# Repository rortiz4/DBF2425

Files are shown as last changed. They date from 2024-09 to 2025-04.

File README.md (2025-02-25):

# DBF2425
Any hardware or software design files for DBF 24-25 will be uploaded here

## Control System Software Flowchart
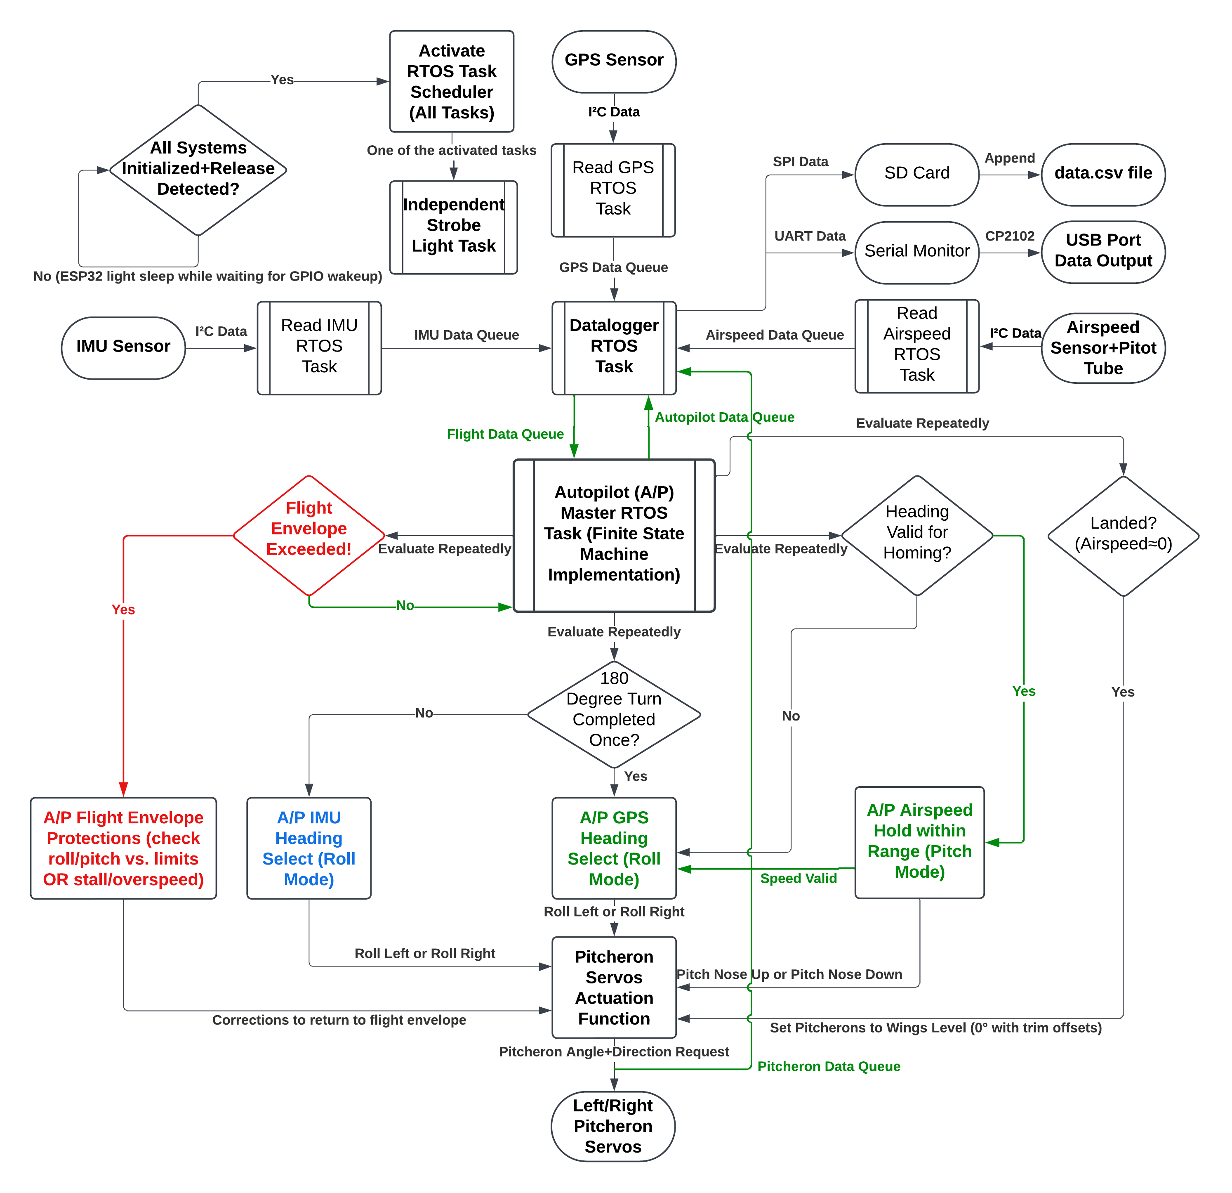
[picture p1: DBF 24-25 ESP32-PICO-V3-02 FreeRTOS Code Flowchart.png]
DBF 24-25 ESP32-PICO-V3-02 FreeRTOS Code Flowchart


## Power Path
DBF 24-25 System Power Path

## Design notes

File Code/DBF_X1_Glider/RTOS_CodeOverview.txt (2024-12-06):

RTOS Features Implemented:
(Sensors):
- IMU
- Differential Pressure (Pitot Tube/Airspeed)
- GPS

CPU Usage:
- CPU0: All sensor reading tasks are on this since they need the I2C Mutex anyway, so only one task runs at a time (no parallel benefit)
- CPU1: Data Logging task since after receiving queue data, it can immediately start saving data while the sensors are collecting the next dataset

Tasks (4, each with 4096 bytes stack size [lower = faster sampling]):
- Initialize All Sensors... Don't need RTOS for this
- Initialize SD Card / Data Logging... Don't need RTOS for this
- Read IMU (CPU0)
- Read Airspeed Sensor (CPU0)
- Read GPS Data (CPU0)
- Log Data to CSV File (CPU1)

Queues (3):
- IMU Data Queue Send => Logging Task Queue Receive
- Airspeed Data Queue Send => Logging Task Queue Receive
- GPS Data Queue Send => Logging Task Queue Receive

Timers: None (Could make one for built-in LED just for fun)

Task Control (Suspend/Resume):
- SUSPEND TASK: IMU Read once queue is filled with fresh data
- SUSPEND TASK: Airspeed Read once queue is filled with fresh data
- SUSPEND TASK: GPS Read once queue is filled with fresh data
- RESUME TASKS ABOVE: As soon as each queue is emptied by logging task => Each Sensor Reading Task (only log after all sensors have been polled once)

Mutex(1) + Binary Semaphores(3):
- I2C Bus MUTEX: Ensures only one sensor accesses the I2C bus at any given time.
Each sensor task attempts to take it once in the infinite loop
While waiting for data, each sensor task gives back the semaphore in a sub-infinite (while !data) loop
If there is data, the semaphore is taken by the sensor that got data
After pulling the data, the semaphore is given back (and task suspends).
- IMU Done Reading Semaphore => Signals Logging Task that queue is filled with fresh data
- GPS Done Reading Semaphore => Signals Logging Task that queue is filled with fresh data
- Pitot Tube Sensor Done Reading Semaphore => Signals Logging Task that queue is filled with fresh data

Files:
- main.cpp: self-explanatory starting point for program (as small as possible but #includes a lot)
- sensors.h+sensors.cpp: Code for initializing Serial, I2C, and all sensors (not with RTOS) + Task Functions to read each sensor individually + structs for each sensor's data/types
- datalogger.h+datalogger.cpp: Code for initializing the SD Card and logging (.csv) data to Serial Monitor and/or SD Card file.
- Tasks, Queues, and Semaphores + their associated handles, declarations, and definitions are stored in tasks.h/tasks.cpp, queues.h/queues.cpp, and semaphores.h/semaphores.cpp

(Outputs):
- SD Card .csv file writing
- Serial Monitor Printing
- LED Toggle after every .csv file entry.

Sample Rate Estimates:
- IMU Alone: 15Hz
- Airspeed Sensor Alone: 145Hz
- All Sensors Together: 10Hz originally (excluding GPS)
- After Optimizations (lower stack size, using dual core, etc.): 15.34Hz rate (excluding GPS)

TODO (as of 12/04/2024):
New Tasks:
- Release Detection: Detect when IOXX has been pulled LOW/HIGH
- Strobe LED: Blink the LED (IOXX)
- 180 Degree Turn (any angle allowed actually): Counter-Rotate Pitcherons. Compares current bearing vs. current bearing-180 degrees
- Level Roll: Counter-Rotate to maintain level flight (+/-5 deg of roll allowed). If bank angle exceeds +/-5 degrees, rotate back to center
- Level Pitch: Rotate pitcherons together to maintain airspeed target (pitch up to slow down, down to speed up)
Note: Level Roll has priority over Level Pitch (semaphore required). Could combine 3 tasks above into 1 Autopilot task.

New Queues:
- Flight Data (source: datalogger task function, sinks: 180 degree turn and level flight OR Autopilot tasks)
- Autopilot Data (source: Autopilot task, sink: datalogger)
- Servo Angle Data (source: actuate_pitcherons in pitcherons_servos.cpp, sink: datalogger task function)

New Semaphores:
- 180 Degree Turn Semaphore (180 degree turn task gives, level roll task takes)
- Level Roll Semaphore (Level roll task gives, Level Pitch task takes)
- OR just ONE Autopilot Done Semaphore for datalogger

New Files:
- pin_map.h: consolidates all physical I/O pin assignments (from PCB schematic)
- pitcherons_servos.h, pitcherons_servos.c: contain code to initialize servos and actuate to an angle (no direct tasks)
Note: servos.h will contain struct to hold servo angle data (int angle and int act_type_direction)
- strobe.h, strobe.cpp: contain code to initialize Addon strobe LED and task function for blinking (+ Data struct)
- autopilot.h, autopilot.cpp: contain task functions that actually perform turns and pitch adjustments based on sensor data.

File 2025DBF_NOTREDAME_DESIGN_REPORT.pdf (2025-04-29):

University of Notre Dame | Page 2 of 60

## Contents

1 Executive Summary | 4
2 Management Summary | 5
3 Conceptual Design | 6
4 Preliminary Design | 15
5 Detailed Design | 32
6 Manufacturing Plan | 48
7 Testing Plan | 53
8 Performance Results | 57
9 Bibliography | 60

University of Notre Dame | Page 3 of 60

## Acronyms and Symbols

α - Angle of Attack

AR - Aspect Ratio

ARV T - Aspect Ratio of the Vertical Tail

β - Sideslip Angle

bW - Wing Span

bHT , bV T - Horizontal, Vertical Tail Spans

CA - Cyanoacrylate (glue)

CAD - Computer Aided Design (Software)

CAM - Computer Aided Manufacturing

CD - Coefficient of Drag

CL - Coefficient of Lift

CLmax
- Maximum Coefficient of Lift

c¯W - Mean Aerodynamic Chord

CHT , CV T - Horizontal, Vertical Tail Coefficients

CF - Carbon Fiber

CG - Center of Gravity

Cm - Pitching Moment Coefficient

Cmα

- Slope of the Cm vs α curve

CNC - Computerized Numerical Control

D - Drag

DBF - Design, Build, Fly

e - Oswald Efficiency Factor

EIH - Engineering Innovation Hub

ESC - Electronic Speed Control

FEA - Finite Element Analysis

FoM - Figures of Merit

g - Acceleration Due to Gravity

GM - Ground Mission

GM - Ground Mission Score

GPS - Global Positioning System

I - Second Moment of Inertia

IMU - Inertial Measurement Unit

LHT , LV T - Horizontal, Vertical Tail Moment Arm Distance

L - Lift

LiPo - Lithium Polymer

M1 - Mission 1

M2 - Mission 2

M3 - Mission 3

M1 - Mission 1 Flight Score

M2 - Mission 2 Flight Score

M3 - Mission 3 Flight Score

MATLAB - Matrix Laboratory

Mmax - Maximum Moment

n - Load Factor

Nc - Number of Aircraft Components

NACA - National Advisory Committee for Aeronautics

ND DBF - Notre Dame Design, Build, Fly

PCB - Printed Circuit Board

PID - Proportional Integral Derivative

PWM - Pulse Width Modulation

Q&A - AIAA Rules Clarification Question and Answer

RC - Radio Controlled

Re - Reynold’s Number

RK4 - 4th Order Runge-Kutta Method

RPM - Revolutions Per Minute

SW - Planform Area

SHT - Area of Horizontal Tail

SV T - Area of Vertical Tail

SM - Static Margin

T - Thrust

V - Airspeed

Vclimb - Climb Velocity

Vland - Landing Velocity

Vs - Stall Speed

VHT - Horizontal Tail Volume Ratio

W - Weight

XCG - x-location of Center of Gravity

XNP - x-location of Neutral Point

XFLR5 - XFoil Low Reynolds Version 5

XPS - Extruded Polystyrene

µ - Kinematic Viscosity

ϕ - Bank Angle

ρ - Density of Air

σ - Bending Stress

τ - Flap Effectiveness Parameter

Λt/c - Sweep of the Maximum Thickness Over the Chord Line ψ˙
- Turn Rate

University of Notre Dame | Page 4 of 60

## 1 Executive Summary

The following report outlines the process followed by the Notre Dame Design Build Fly team to prepare for entry into the 2025

American Institute of Aeronautics and Astronautics Design/Build/Fly Competition. The team has designed and built a radio-

controlled aircraft and an X-1 test vehicle to complete three flight missions and one ground mission, as described in the AIAA

competition rules [1]. To achieve this, the main aircraft was optimized to carry a large payload for Mission 2 and to have high

endurance for Mission 3. The X-1 test vehicle was designed to execute a flight path to land in the maximum scoring zone.

The main aircraft features a low wing design with a puller configuration and tail dragger landing gear. The empennage consists

of a conventional tail connected to a tapered section of the fuselage by a boom. The low wing design was selected to maximize

maneuverability, while a dihedral wing angle was incorporated to improve stability. The single motor puller configuration was

chosen for its efficiency and minimal interference with mission objectives. A tail dragger configuration was chosen for its reduced

weight and drag, and the boom tail further minimizes weight and surface drag from the rear section of the aircraft. The fuselage

cross section is a Norman window shape, providing both a simplified interface for external components and reduced drag with

its curved roof. This configuration is shown in Figure 1. The fuselage and wings are primarily constructed from wood due to

its lightweight properties and ease of manufacturing. Select structural components, such as the spars and boom tail, are made

from carbon fiber, while the wingbox is machined from aluminum. Removable pylons can be attached to the wing tips to hold fuel

tanks, which are loaded with a combination of concrete powder and steel weights. The X-1 test vehicle is attached to the bottom

of the fuselage below the wingbox, with its vertical stabilizer passing through a bomb bay door in the fuselage floor. This location

was chosen to minimize shifts in the aircraft’s center of gravity when the vehicle is dropped. The X-1 test vehicle has a low wing

configuration with a conventional tail, both chosen for their reliable stability and low weight, and is controlled by a custom system

that rotates the wings to function as either ailerons or an elevator. Control inputs are informed by a GPS, an IMU, and a Pitot

tube. The X-1 test vehicle is constructed from carbon fiber and foam to minimize weight.

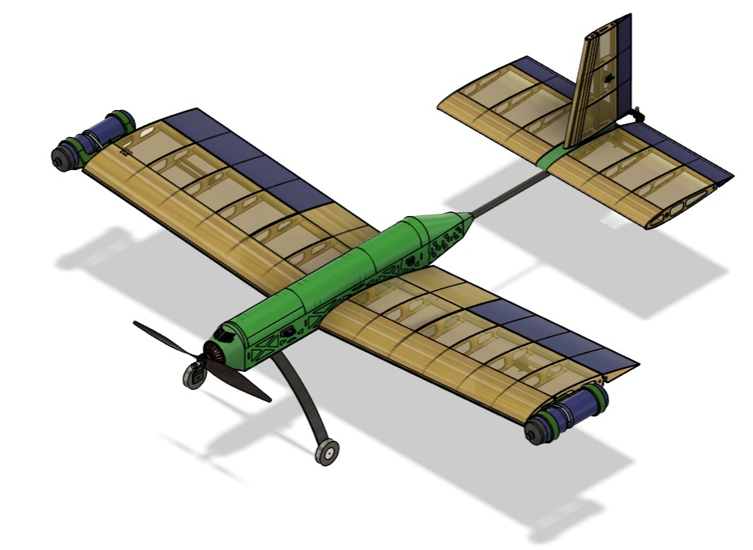
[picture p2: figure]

Figure 1: ND DBF 2025 Aircraft

Scoring analysis was conducted to determine the optimal air-

craft configuration for maximizing payload weight, lap time for

M2, and endurance for M3. Following scoring analysis and

considering lessons learned from test flights, the team chose

to carry a 8 lb payload and have a total flight time of 87 sec-

onds for M2. For M3, the aircraft is designed to complete 9

laps, with the X-1 test vehicle weighing 0.29 lbs to aim for the

2.5-point bonus zone. The pylons and X-1 attachment mech-

anism were designed to minimize installation time for a higher

GM score while remaining securely attached throughout the

flight. To improve on detailed designs the team planned five

flight tests of iterative aircraft. In addition, structural and

propulsion tests were planned to inform performance of spe-

cific components. Early flight tests led to a major redesign to

improve the landing performance of the aircraft. Subsequent

tests have demonstrated that the current design track is able

to perform and excel in all scoring missions.

University of Notre Dame | Page 5 of 60

## 2 Management Summary

### 2.1 Team Organization

Figure 2: Team Organizational Structure

The Notre Dame DBF team consists of approx-

imately 25 undergraduate members, with about

15 returning and 10 new members. The overall

organizational structure of the team is illustrated

in Figure 2. The general membership of the team

is divided into three main design squads: Aerody-

namics, Structures and Manufacturing, and Pay-

load. The Aerodynamics squad is responsible for

the aerodynamic parameters of the plane, includ-

ing lifting surface design, propulsion design, and

stability analysis. The Structures and Manufac-

turing squad is responsible for the structural in-

tegrity of all components, fuselage design, and

manufacturing process selection. The Payload

squad is responsible for all payload systems,

avionics, and mechanisms necessary for mission completion. It is notable to mention that the X-1 test vehicle design is shared be-

tween the three squads rather than being a payload-specific task. Each squad is run by a lead who is responsible for conducting

meetings and ensuring that squad-specific design requirements are met in a timely manner. The Structures and Manufacturing

squad is managed by co-leads to handle the large number of responsibilities and to provide mutual support and oversight. Each

squad lead is supported by sub-leads, who act as assistants for leads instead of having specific tasks. Sub-leads help with both

design and administrative tasks, ensuring the smooth operation of the squad and serving as reliable team members. All three

squads are overseen by the Project Manager and the Chief Engineer. The Project Manager is responsible for keeping the team on

schedule, within budget, and focused by setting team goals, managing budget constraints, organizing meetings, and purchasing

supplies. The Chief Engineer oversees top-level requirements and makes all final design decisions. The Chief Engineer also

provides design requirements to the squads, and the Project Manager ensures those requirements are efficiently completed. The

whole team is advised by Industry and Faculty advisors during design reviews. Additionally, the team receives empirical feedback

from a non-student pilot during test flights. The team also includes several auxiliary roles to address areas of past weaknesses.

The Research and Development Officer is responsible for enhancing the team’s performance potential by improving subsystems

and processes. The Chief Technical Editor oversees the organization of all reports and proposals. The Media Editor manages

the team’s social media presence and recruits new members.

### 2.2 Milestones

The Project Manager holds the team to the schedule outlined in Figure 3. Squad tasks are completed during weekday meetings,

and a full team meeting is held on Sundays to maintain communication between squads. The schedule has been adjusted

throughout the year, mainly due to flight tests that resulted in minimal structural damage. This led to small repairs and flights

being moved to the following week to collect more information.

University of Notre Dame | Page 6 of 60

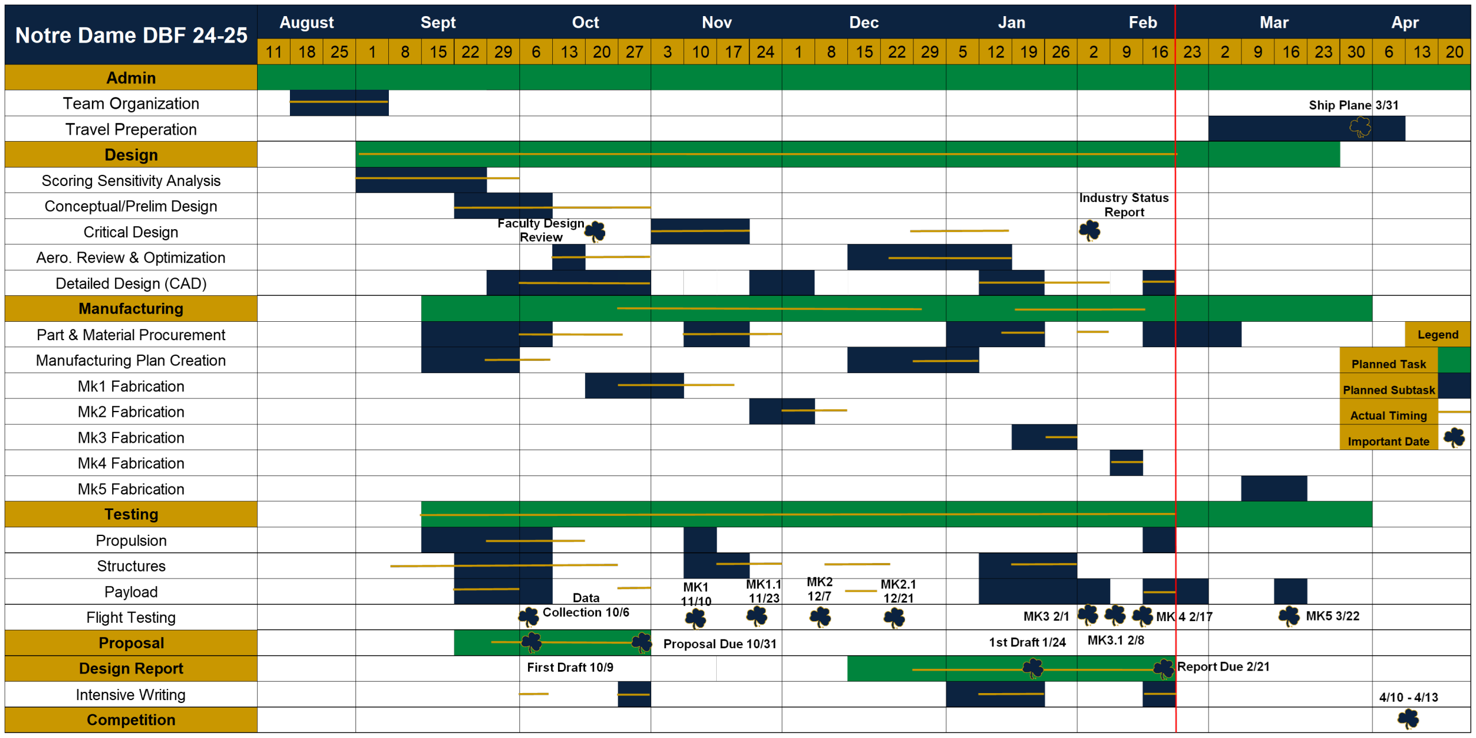
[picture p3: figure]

Figure 3: 2024-2025 Gantt Chart

## 3 Conceptual Design

### 3.1 Engineering Requirements

ND DBF’s engineering requirements were developed using a careful analysis of mission requirements, obtained through a thor-

ough review of the rules and Q&As released by AIAA.

### 3.1.1 Problem Statement

ND DBF must design, build, and fly an airplane to execute an X-1 Supersonic Flight Test Program, completing three assigned

flight missions and a ground mission in order to ensure airworthiness, test payload capacity and speed, and demonstrate the

ability to effectively deploy an X-1 test vehicle from the main aircraft.

### 3.1.2 General Aircraft Requirements and Restrictions

AIAA has provided comprehensive guidelines through the official rules and subsequent Q&A sessions. These guidelines outline

design constraints, performance expectations, and payload regulations for the ND DBF team. Table 1 details the requirements

that the team considers central to the aircraft design and their impact on each ND DBF squad.

University of Notre Dame | Page 7 of 60

Table 1: Mission Requirements and Squad Impact

Category | Requirement | Aerodynamics Squad | Struct. & Manu. Squad | Payload Squad
Aircraft Design | The maximum airplane wingspan is six feet. | Design tradeoff between wing area and aspect ratio. | The structure must endure a maximum span of six feet. | Minimal Implications.
| Aircraft must be capable of completing all three missions. | Plane aerodynamic design must allow completion of all three missions. | Plane structural design must allow completion of all three missions. | Payload design must allow completion of all three missions.
| Aircraft must be flown in same configuration for all three missions excluding payloads. | Aerodynamic design must complete all three missions without changes. | Structural design must complete all three missions without changes. | Payload design must complete all three missions without changes.
| No structure or components may be dropped from the plane during flight excluding the X-1 test vehicle in M3. | Minimal Implications. | No loose components are permitted. | X-1 test vehicle must be secured when attached to main aircraft.
| Commercially available propeller, battery, and motor must be used. | Only commercially available propulsion systems can be considered for the aerodynamic design. | Minimal Implications. | Minimal Implications.
| Aircraft must pass a wing tip test in the heaviest flight condition. | Minimal Implications. | Plane structural design must pass a wing tip test at maximum flight weight. | Minimal Implications.
| Aircraft can be any configuration other than rotary and lighter than air. | Aircraft must be designed with traditional fixed wings. | Minimal Implications. | Minimal Implications.
Assembly | Assembly work on the aircraft must be completed with the plane in the upright, parking position. The aircraft cannot be picked up, rotated, or put in any other position. The only exception to this is the ability to add blocks underneath the wheels of the landing gear to allow for access underneath the plane if need be. | Minimal Implications. | Structural members and hatches must be placed carefully to facilitate assembly and loading in the upright configuration. | Payload components must be designed and placed to facilitate assembly and loading in the upright configuration.
| Aircraft will enter the staging area in the parking configuration with the propulsion battery and payload removed. Aircraft assembly and payload installation must be completed in less than five minutes by one person. | Minimal Implications. | Structural members and hatches must be placed carefully to facilitate assembly in less than five minutes. | Payload components must be designed and placed to facilitate assembly and loading in less than five minutes.
Flight Performance | Aircraft must have a successful landing to receive a score for the mission. | Aircraft must be designed to land at a velocity that is controllable for the pilot | Structure must withstand the force of landing without failure | Minimal Implications
| The airplane will use ground rolling takeoff and landing. | Wing, propulsion system, and weights must be selected to allow for rolling takeoff. Must take off in length of testing runway. | Aircraft structures must withstand the forces of extended takeoff and landing. | Minimal Implications.
| Fuel tanks can be any commercially available bottle as long as it has a screw-on lid. Bottle can be painted/decorated, but otherwise cannot be altered in any way. Bottle must have a minimum capacity of 16 oz. Bottle cannot be glass. | Bottle chosen must be as aerodynamic as possible. | Minimal Implications. | Fuel tank must be designed to meet the requirement.
| Fuel tank bottles can be filled with any amount of inert material to get the desired payload weight. | Design tradeoff between fuel tank weight and speed. | Minimal Implications. | Fuel tank must be strong enough to hold intended payload weight.
| At least two fuel tanks must be carried externally (minimum of 2 fuel tanks required). External fuel tanks must be identical. Internal fuel tank can differ from external. Internal fuel tank is optional. | Minimal Implications. | Fuselage and wings must be designed to withstand additional weight from fuel tanks. | Fuel tanks must be designed to be properly incorporated with aircraft, whether internal or external.
| External fuel tanks must be attached using detachable pylons. Pylons must hold fuel tank securely for all phases of flight. | Pylons should be as low-drag and light as possible since their weight will not affect mission score. | Minimal Implications. | Pylons must be secure enough to hold fuel tanks through all phases of flight. Also must design pylons to be detachable. Fuel tanks chosen must interface properly and securely with pylon.
| X-1 test vehicle must be attached to the plane and dropped at an altitude of 200-400 ft via command from the transmitter. | Minimal Implications. | Minimal Implications. | Must design a low-weight mechanism to hold and release the X-1 test vehicle on command/at altitude.
| Fuel tanks must be placed on either side of the X-1 test vehicle. | Minimal Implications. | Minimal Implications. | Fuel tank placement must be chosen properly to meet the requirement.
| After being dropped, the X-1 test vehicle must achieve stable flight after release from the airplane, execute a 180 degree turn, and then fly a descending pattern or orbit until landing on the ground. | X-1 test vehicle must be designed to achieve steady flight and required flight path. | Minimal Implications. | A mechanism for controlling the X-1 test vehicle must be designed to achieve flight requirements.
| X-1 test vehicle must have flashing lights/strobes which turn on only after release from plane and remain on through landing. Lights must be easily visible to flightline judge. | Minimal Implications. | X-1 test vehicle must protect necessary components for strobe light operation through landing. | X-1 test vehicle must be designed to meet this requirement.
| X-1 test vehicle cannot exceed 0.55 lbs in weight. | X-1 test vehicle aerodynamic surfaces must be light while still maintaining control authority. | Materials chosen for X-1 test vehicle must be light but strong enough to withstand flight loads. | X-1 test vehicle components and total weight must remain under 0.55

Payload

lbs in weight. 3.1.3 Mission Scoring Summary

AIAA has outlined the mission rules and scoring criteria. A brief description of the requirements for each mission, along with the

associated scoring equations, is shown in Table 2.

University of Notre Dame | Page 8 of 60

Table 2: Mission Scoring Summary

Mission | Description | Scoring
GM | Record time to install pylons, X-1 test vehicle with attachment mechanism, and fuel tanks. Verify function of all control surfaces and X-1 test vehicle release function. Aircraft enters staging area in M1 configuration before timer begins.
M1 | Delivery flight with no payload. Complete 3 laps of flight course within 5 minute time window. Complete a successful landing.
M2 | Captive carry flight with loaded fuel tanks and X-1 Vehicle payload. Complete 3 laps of flight course in shortest possible time. Carry X-1 and fuel tanks for duration of flight and successfully land.
M3 | Launch flight with unloaded fuel tanks, X-1 test vehicle, and payload. Complete maximum number of laps in 5 minute window. At beginning of final lap drop X-1 test vehicle prior to the upwind turn. Once dropped X-1 test vehicle must complete a 180° turn before landing in bonus point area. X-1 test vehicle strobe light must be on during descent and after landing, but never before. Primary aircraft must complete a successful landing.

### 3.1.4 Competition Scoring Summary

Table 3: Participation Scoring

Participation Score | Requirement

## 1 Attend Fly-off 2 Pass Tech Inspection 3 Attempt Flight Mission

The overall competition score is a combination of Mission Score, Report Score, and

Participation Score, P, further detailed in Table 3. Of note is that the Total Mission

Score is multiplied by the Report Score. The larger variance in Mission Score

means that it has a larger effect, however, the Report Score acts as a multiplier on

the performance of the team during the missions. The Total Report Score is split

into components for the proposal and design report as described in Equation (2).

Competition Score = Total Report Score × Total Mission Score + P | (1)
Total Report Score = (0.15 × Proposal Score) + (0.85 × Design Report Score) | (2)
Total Mission Score = M1 + M2 + M3 + GM | (3)

### 3.2 Scoring Sensitivity Analysis

After breaking down mission requirements into specific aircraft design criteria, the team analyzed this year’s critical scoring

parameters to optimize the wing and propulsion system for maximum performance. Using a MATLAB script, potential aircraft

configurations were generated by fixing the wingspan at the maximum allowable 6 ft and iterating over the wing aspect ratio

and payload weight [2]. Fixing the wingspan at 6 ft allowed for the design of efficient, high aspect ratio platforms, but was later

altered to accommodate the payload fuel tanks being attached at the wingtips. To account for scoring dependence on landing

location and weight, the X-1 test vehicle was treated as an additional 0.55 lbs in the total aircraft weight. The script estimated the

structural and electronics weights based on previous DBF aircraft and selected a propulsion system using a custom database of

manufacturer-provided data for motors, propellers, and batteries. Each configuration of aspect ratio, motor, propeller, and battery

was required to achieve three primary goals:

1. Attain a minimum static thrust-to-weight ratio of 1.2.
2. Fly for at least 5.5 minutes.
3. Take off within 250 ft (the length of the team’s test runway).

University of Notre Dame | Page 9 of 60

The thrust-to-weight ratio was chosen from a historical range of 0.8 to 1.2, with the upper limit selected to ensure sufficient

thrust to offset the added drag from the fuel tanks. Configurations meeting these criteria were deemed minimally viable for the

competition. Each viable configuration was mathematically simulated and scored using the M2 and M3 scoring equations, as well

as performance equations from Thomas Corke’s Design of Aircraft [3]. Figure 4 shows the flow of the scoring analysis script. The

results, illustrated in Figures 5 and 6, show each point representing a viable aircraft and propulsion configuration.

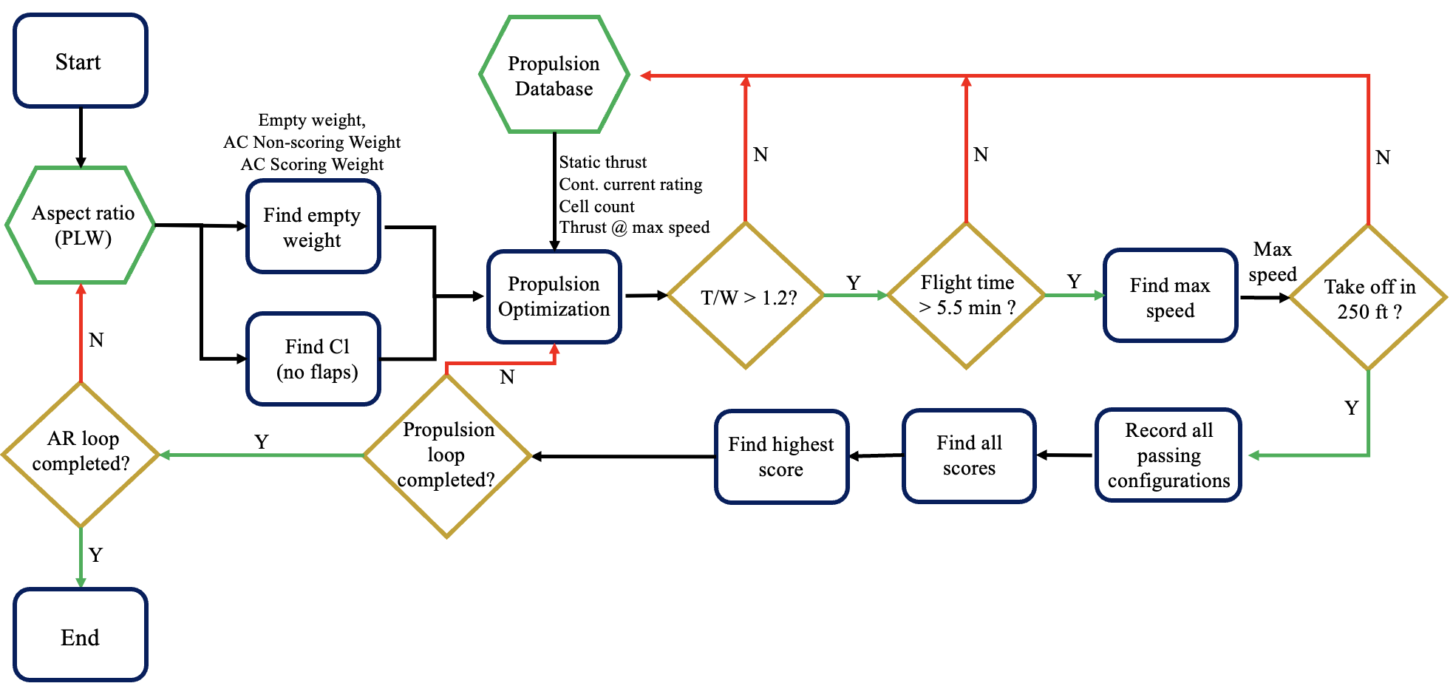
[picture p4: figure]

Figure 4: Flow Chart of ND DBF’s Scoring Analysis Script

After preliminary testing flights with failures resulting from an excessively high required landing speed, it was determined that

the original scoring strategy did not adequately take into account pilot controllability factors such as landing speed. Thus, the

scoring analysis code was altered to implement penalties for high landing and takeoff speeds. This was done by requiring

each configuration to have a maximum stall speed of 40 ft/s and capping the maximum wing area to 7.5 ft²
, both of which

were determined through ND DBF’s previous experience with successful flights, best manufacturing practices, and conventional

wisdom regarding RC aircraft. Once these penalties were implemented to ensure the selected design would be flyable by a pilot,

Figures 5 and 6 were created. Due to budget constraints, the team was unable to select a new motor for the aircraft and thus

decided to map the current motor to a new, winning configuration. In both figures, each minimally viable aircraft is plotted by its

maximum speed, determined by calculating the excess thrust of each aircraft and the speed at which it is minimized. For the

selected aircraft, the maximum velocity for each mission is indicated by a red X. However, cruise speed values, defined as the

flight speed when lift is equal to weight without any additional pitch control input, are generally much lower than the maximum

speed. The cruise speeds for each mission were calculated using Equation (4), where lift is assumed to equal aircraft weight.

L = W =

1
2
ρV ²CLSW | (4)

These values are shown for the given aircraft in Figures 5 and 6 as a black X. These velocity values are low relative to the

maximum velocity of the aircraft. However, based on previous year’s flight data, the team has determined that, by taking advantage

of pitch control and diving capability, the pilot can exceed this cruise value to roughly 95% of the maximum velocity of the aircraft.

This value, marked by the golden star in Figures 5 and 6, is the predicted competition lap velocity and is used for a majority of the

following analyses. The final results of the scoring analysis, including performance predictions and physical design parameters,

are shown in Tables 4 and 5.

University of Notre Dame | Page 10 of 60

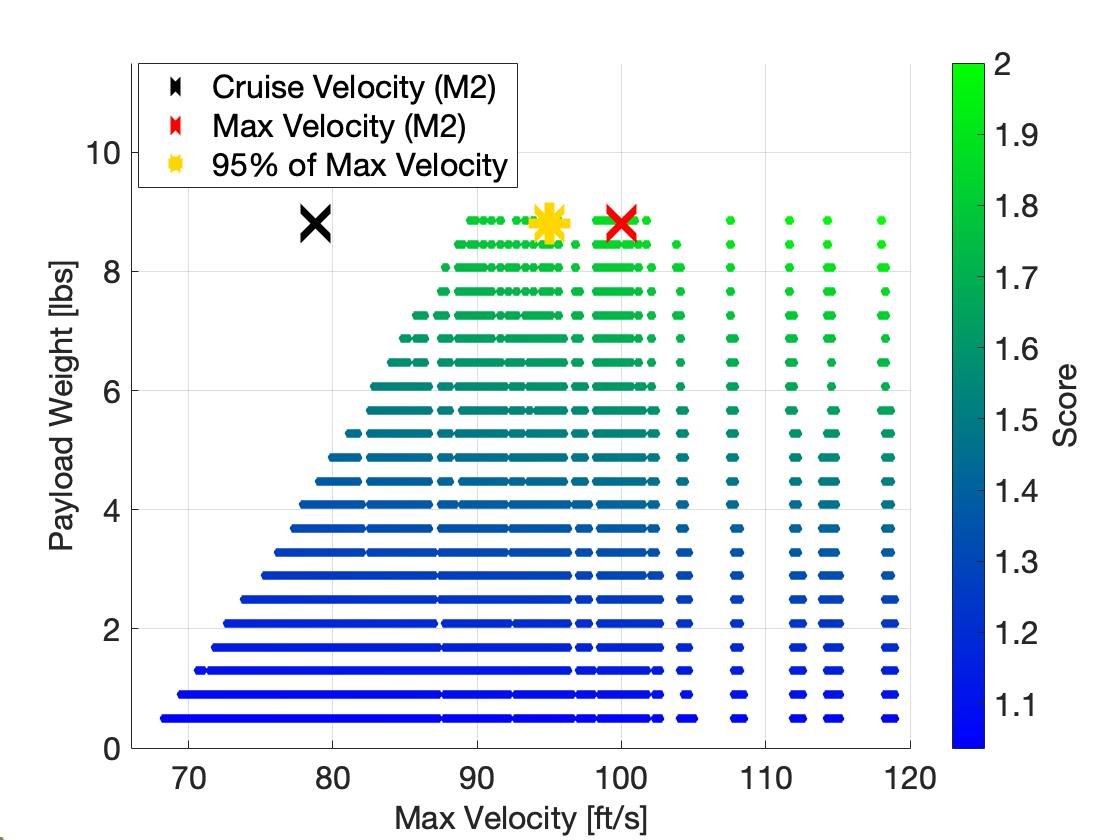
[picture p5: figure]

Figure 5: ND DBF M2 Scoring Analysis | Figure 6: ND DBF M3 Scoring Analysis

Table 4: Preliminary Scoring Parameters

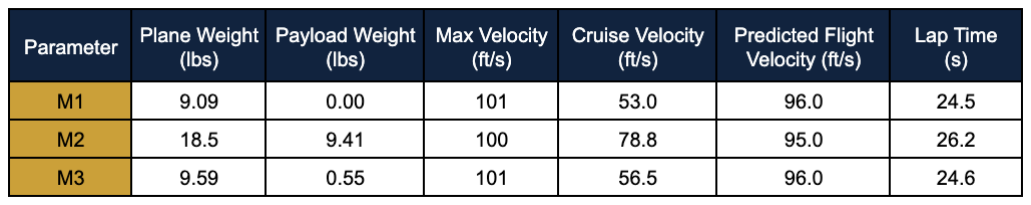
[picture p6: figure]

Table 5: Preliminary Design Parameters

### 3.3 Concepts Selection Process

To select the overall aircraft configuration, including the wing and empennage designs, the team utilized weighted decision

matrices to evaluate various options against Figures of Merit (FoM) determined by the design requirements. Every design option

was rated on a scale of 1 to 5 for each FoM, with the highest total score, a sum of the individual FoM scores multiplied by their

respective weights, representing the best choice. The assigned weight and scores were selected based on knowledge from

the team’s past airplane performance, additional research, and the performance of other teams’ past aircraft, with the selected

configuration for each decision matrix marked by a filled green box.

### 3.3.1 Overall Aircraft Configuration Trade Study

To ensure a successful design, it was crucial for the team to choose an overall configuration that was most suited for the challenges

of this year’s competition. This was accomplished using the trade study shown in Table 6. As such, out of the five FoM utilized in

Table 6, mission capability (as determined by a configuration’s ability to meet more specific design criteria outside of weight, drag,

and maneuverability) was weighted the highest, followed closely by manufacturability to ensure prudent decisions were made

about the team’s capabilities. Three options were considered: a monoplane, a biplane, and a blended wing. While the blended

wing performed marginally better in mission capability, it was deemed far more difficult to manufacture than other designs, limiting

the team’s ability for rapid prototyping. The biplane was far more comparable to the monoplane, but was not chosen due to its

University of Notre Dame | Page 11 of 60

lower drag and manufacturability scores. Instead, the monoplane configuration was chosen as a reliable, well-tested configuration

that performed well across the board and lent itself more towards rapid prototyping opportunities with its greater manufacturability.

Table 6: Overall Aircraft Configuration

### 3.3.2 Wing Configuration

Table 7 includes the following wing configurations: high wing, low wing, and mid wing. Drag and weight were given the highest

weightings in the FoM because of the effect of the external fuel tanks on the speed and flight capability of the plane in M2 and

M3. Manufacturability was given equivalent importance to drag and weight because of the strict time considerations necessary

to allow for frequent redesigns. The mid wing design was not selected because of manufacturability concerns and the additional

weight it would require to provide support at the middle of the fuselage. While the high wing generally has a higher lift-to-drag ratio

and better dynamic stability, the low wing was selected for its manufacturability and its greater maneuverability at high speeds.

Table 7: Wing Configuration

### 3.3.3 Empennage Configuration

Table 8 shows the five configurations considered for the main aircraft tail and the FoM used. The trade study considered five

FoM, with mission capability, drag, and manufacturability weighted equally the highest. The V-tail had many benefits in terms

of reducing drag, reducing weight, and increasing maneuverability, but, like the H-tail, there were concerns about the difficulties

of manufacturing. Additionally, the cruciform, T-tail, and H-tail configurations would need more internal supports, and would

therefore weigh more than a conventional tail. For these reasons, a conventional configuration was chosen for its high ease of

manufacturability, mission capability, and reliable performance in stability and maneuverability.

University of Notre Dame | Page 12 of 60

Table 8: Empennage Configuration Trade Study

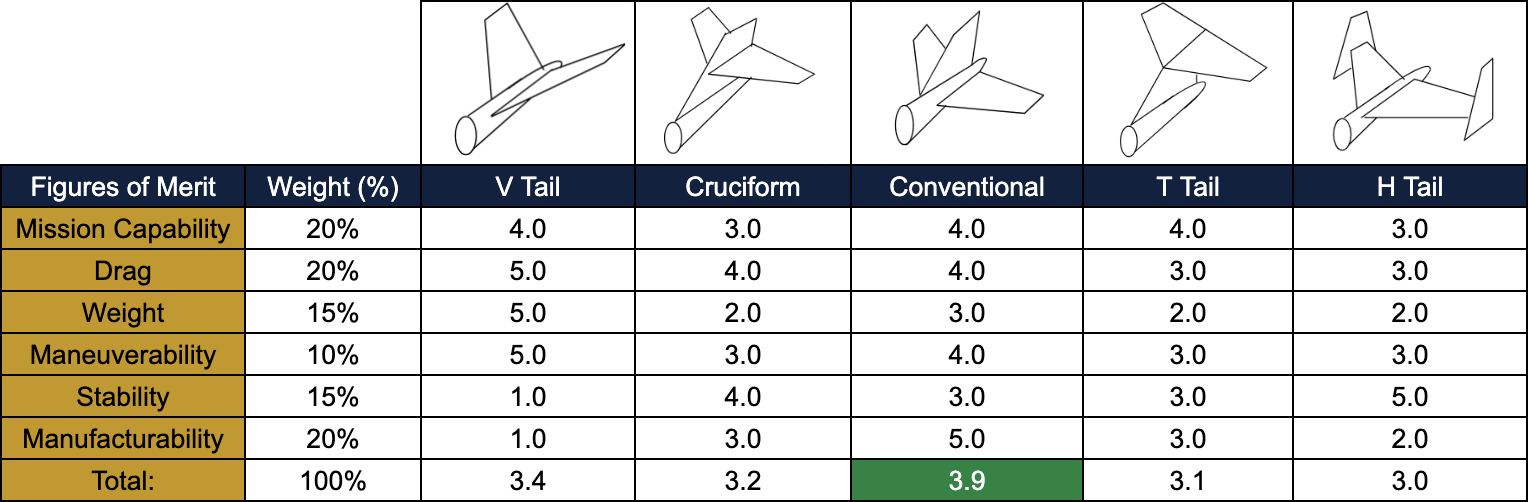
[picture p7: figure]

### 3.4 Aircraft Component Selection, Processes, and Results

### 3.4.1 Propulsion

Four potential configurations, detailed in Table 9, were considered for the propulsion system. Five FoM were used to evaluate

the configurations, with unique weightings attributed to each based on their importance to mission performance. A pusher

configuration would weigh roughly the same as the puller, but the motor position would reduce the motor efficiency due to

disturbed airflow from the fuselage and tail. Additionally, the pusher design came with concerns that a dropped X-1 test vehicle

may collide with a propellor extending below the fuselage behind the X-1 test vehicle at high speeds. Additionally, the dual-

motor and pusher-puller configurations introduce concerns with weight, as both would require a second motor with additional

supports, as well as greater complexity in manufacturing which could result in added failure points during flights. Ultimately, a

puller configuration was chosen due to its high efficiency, low weight, and ease of manufacturability. Although there were concerns

with the induced drag of the design, these were outweighed by the aforementioned benefits.

Table 9: Propulsion System Design Trade Study

### 3.4.2 Landing Gear Configuration

Three landing gear configurations were considered for the main aircraft: tricycle, tail dragger, and bicycle. Initially, the tricycle

configuration was chosen from the trade study due to its greater stability and the ease with which the payload could be mounted.

Additionally, the idea of a retractable landing gear was pursued in order to reduce drag. However, due to difficulties with hard

landings and the retracting mechanism, the team decided against the tricycle configuration and switched to a tail dragger. This

configuration would weigh significantly less, offer reduced drag compared to a non-retractable tricycle gear, and protect the

propeller from rough landings. All considerations that are reflected in the updated trade study are shown in Table 10, in which

figures of merit have been reevaluated to reflect the team’s findings.

University of Notre Dame | Page 13 of 60

Table 10: Landing Gear Configuration Trade Study

### 3.5 Payload Configuration Trade Studies

### 3.5.1 External Fuel Tank Properties

The team considered four shapes of bottles for the external fuel tanks shown in Table 11: standard ribbed, bullet, box, and tapered

midsection. The FoM accounted for included aerodynamic efficiency, ease of attachment to the plane, and filling efficiency of each

bottle. Of these, aerodynamic efficiency was determined to be of the greatest importance, with filling efficiency determined of the

least importance. The standard ribbed bottle had average scores but did not perform the best in any category. The box bottle

scored similarly; though its higher cross-sectional area resulted in a lower aerodynamic efficiency score. The bullet shaped bottle

had high scores in aerodynamic efficiency and filling, but its smooth body limited interfacing ability with the pylon, causing its ease

of attachment score to be lower. The tapered midsection bottle was ultimately selected due to its high aerodynamic efficiency

score relative to the other bottles and because its tapered shape greatly increased its ease of attachment to the aircraft.

Table 11: External Fuel Tank Shape Trade Study

The bottle material was selected to be plastic instead of aluminum due to its lighter weight and greater commercial availability.

The fuel tanks were filled with powdered concrete mix and steel weights evenly interspersed throughout. Initially, the team chose

a design with the pylons on the underside of the wing at the wing tip. However, after further iteration and testing, a design that

attaches to the wing tip, parallel to the chord line, was developed. This position was ultimately chosen as it greatly improves the

ease with which the pylon can be removed.

### 3.5.2 X-1 Test Vehicle Control System

For the test vehicle control system used to initiate the strobe lights after release, perform a 180 degree turn, and land in the

2.5-point bonus box, the team considered an off-the-shelf autopilot module, a custom PCB and autopilot software, and an X-1

test vehicle with its control surfaces in a fixed position for a spiraling flight path, as shown in Table 12. Controllability, weight of

the control system, manufacturability, and compatibility with the vehicle frame were the five FoM weighed against each system in

University of Notre Dame | Page 14 of 60

consideration. A custom PCB and software were chosen because they provided the most control over the vehicle’s flight path,

could be customized to fit any airframe, and the tools and technology required to manufacture and assemble the board were

available at Notre Dame’s EIH. While a fixed control surface aircraft would be the lightest solution, it promised no reliability with

its flight path, with the risk of not completing the 180° turn requirement in the face of unpredictable wind gusts. The off-the-shelf

autopilot module was not chosen because it would require the team to build the vehicle around the module’s geometry, potentially

adding weight. The lack of customizability also presents itself within the autopilot program, as the team would be limited by the

provider’s intended use of the autopilot. The custom PCB and software were ultimately chosen due to their customizability with

the physical system and autopilot, despite the added complexity of fabrication and assembly.

Table 12: X-1 Test Vehicle Control System Trade Study

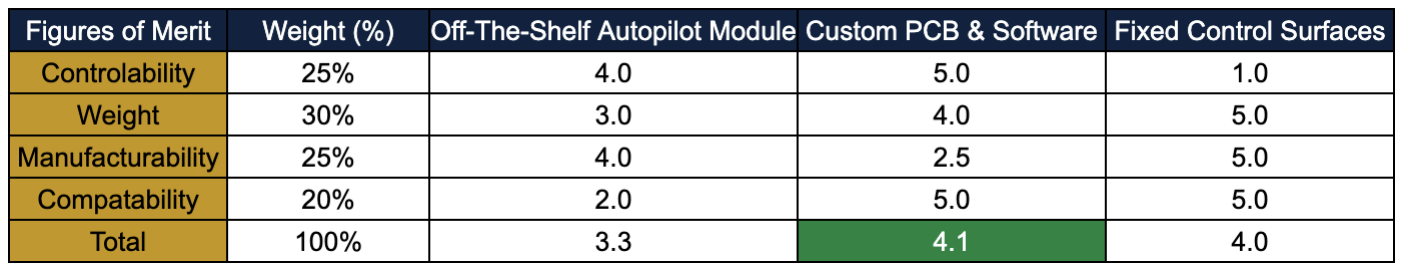
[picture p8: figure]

### 3.5.3 X-1 Test Vehicle Control Surfaces

The team evaluated the possibility of equipping the X-1 test vehicle with a variety of control surface configurations, detailed below

in Table 13. These configurations were judged based on three FoM: weight minimization, control provided, and manufacturability.

Minimizing weight was given the highest priority due to its direct contribution to scoring. It was followed closely by control, to

ensure the X-1 test vehicle could properly satisfy mission requirements for a 180 degree turn, alongside manufacturability to

ensure the design was feasible for the team to construct. Utilizing only full wing control surfaces allow for significantly less weight

than other configurations by reducing the number of servos required for control surface actuation. A configuration using ailerons

and an elevator would yield the greatest relevant control, providing authority over pitching and rolling movements that contribute

directly to the vehicle’s ability to turn and control its descent. While a rudder would allow the vehicle to compensate for adverse

yaw experienced during the turn, this was deemed a relatively low effect for the scale and duration the X-1 test vehicle is operating

over. Utilizing only wing control surfaces as ailerons and flaps would only provide control over roll, as well as some pitch control

if the center of gravity is positioned significantly ahead of the wing. This configuration, while providing less control, offers the

greatest manufacturability by using the fewest control surfaces. Since the X-1 test vehicle does not generate thrust, pitch and

yaw control do not significantly impact the orbiting motion of the vehicle to achieve the 180 degree turn. Therefore, ailerons were

deemed the only significant control surface to perform the turn, and reduced pitch control from moving the wings symmetrically

was deemed effective in this application given a sufficiently nose-heavy vehicle. With these considerations, the team chose to

implement only main wing control surfaces acting as both ailerons and flaps, favoring the low weight and simpler manufacturability.

Table 13: X-1 Control Surface Trade Study

University of Notre Dame | Page 15 of 60

### 3.6 Final Conceptual Design

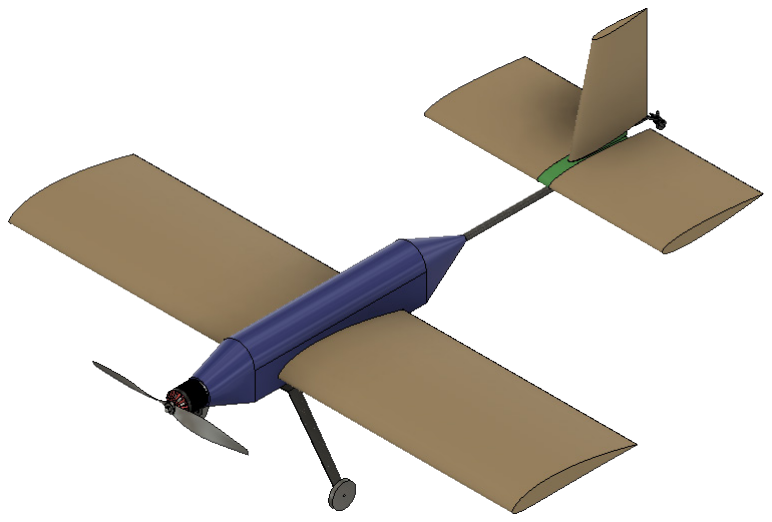
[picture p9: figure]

Figure 7: ND DBF Aircraft Conceptual Design

The final conceptual design of the plane is of a low rectangular

wing monoplane with a 5.33-foot wingspan, an aspect ratio of

3.82, and a single propeller propulsion system. The plane has

a conventional tail attached by a boom to the fuselage, and tail

dragger landing gear. The design decisions determined by the

trade studies, including lighter landing gear and a rectangular

wing, allow for a plane that is more maneuverable and capable

of completing the year’s missions. Figure 7 models the team’s

aircraft conceptual design.

## 4 Preliminary Design

The preliminary design phase focused on generating, collecting, and analyzing data to guide design decisions. The team used a

variety of software tools and applied theoretical equations from existing literature to support the iterative design process.

### 4.1 Design Methodology

The team’s design methodology is detailed in the flow chart below. Beginning with the conceptual design, the team used MATLAB

R2024b [2] to create a scoring analysis code, which is described in Section 3.2 and outputs basic parameters for the highest-

scoring aircraft out of all viable competition configurations. This scoring analysis code provided a basis for the preliminary design

as well as a guide for which optimization parameters yield the highest scores. Because of this, the scoring analysis code was

revised and revisited several times throughout the design process to inform optimization and guide design changes. Given the

initial parameters output from the code, component trade studies were conducted as detailed in Section 3.3. This analysis led to

the initial conceptual design. These semi-qualitative decisions were modeled in the preliminary design phase using XFLR5 [4]

and OpenVSP [5], software packages that generate advanced aerodynamic and performance analyses of the aircraft, including

component placement, CG analysis, and stability calculations, which are detailed in the following section.

Next, the team entered the detailed design phase, which included CAD of the aircraft components and assembly, as well as

structural analyses of critical points on the aircraft using FEA. Once the aircraft was modeled and analyzed to ensure structural

integrity, the team manufactured a prototype of the aircraft using the various methods described in Section 6.2. Team members

performed various tests on the prototype, including flight tests to simulate competition missions and component tests, all of

which are described in Section 7. Finally, the team conducted a thorough analysis of all collected data to gain insight into the

performance of the aircraft, discussed in Section 8. The team repeated this process to improve each subsequent iteration,

referencing and correcting the scoring analysis code to inform design decisions, until a final design was reached. Figure 8

illustrates the flow of this process. To date, the team has completed four prototypes and improved the design with each version.

University of Notre Dame | Page 16 of 60

Figure 8: ND DBF Design Methodology

### 4.1.1 Aerodynamic Critical Parameters

### 4.1.1.1 Wing Span & Aspect Ratio

The wingspan must fit within the 6 ft maximum, as per AIAA rules. Additional constraints on the maximum wingspan include the

positioning of fuel tanks on the wingtips, which the team balanced against the aircraft’s aspect ratio, to achieve greater lift and

increase aircraft efficiency. Higher aspect ratios, which increase with longer wingspans, also result in greater stability at the cost

of maneuverability, a feature deemed to be a necessary tradeoff to ensure safe flight while loaded with high payload weights.

### 4.1.1.2 Wing Area

To carry a heavier fuel tank payload, which directly improves M2 performance, the team desired a high wing area to ensure greater

lift forces. However, a greater wing area can also lead to high skin friction drag and structural concerns as lift forces increase. As

discussed in Section 4.2.1 and Section 4.4.5, the team balanced a multitude of constraints on wing area to determine an optimal

sizing that directly related to the team’s goals for payload weights.

### 4.1.1.3 Airfoil

Several airfoils were considered for the main wing. Each of these were analyzed in XFLR5 to gain accurate predictions of the

airfoils’ properties, including coefficients of lift and drag as well as glide slope predictions and stability parameters. Detailed

explanations of the team’s considerations and decisions can be found in Section 4.2.4.

### 4.1.1.4 Component Location & Stability

Given the impact that payload weight has on the location of the aircraft’s center of gravity, the team positioned payload components

as close to the desired center of gravity as possible to ensure minimal adjustments in center of gravity between missions. The

team used XFLR5 to determine the static margin and various stability metrics and inform component placement decisions.

### 4.1.2 Control Surface Critical Parameters

### 4.1.2.1 Flaps and Ailerons

The team chose not to implement independent flaps due to the lack of restriction on takeoff distances for this year’s competition,

allowing for reduced aircraft weight and system simplification by minimizing the required number of servos for control surface

actuation. Instead, the sole control surface on the wings will be the ailerons, which will be crucial for providing control over the

aircraft’s roll. These ailerons were placed starting from the wingtips to maximize the rotational moment generated, which was

also dependent on the total area of the ailerons and their angle of deflection.

University of Notre Dame | Page 17 of 60

### 4.1.2.2 Elevator

The elevator’s effectiveness is dependent on having a large enough surface area and actuation angle to produce a significant

pitching moment as it alters the effective camber of the horizontal stabilizer, allowing pilot input to control the pitch of the aircraft

around the lateral axis. This pitching moment is also dependent on the distance from the elevator to the center of gravity.

### 4.1.2.3 Rudder

Rudder effectiveness depends on total area, maximum deflection angles, and distance from the aircraft’s center of gravity. Rudder

deflection enables the pilot to adjust the aircraft’s yaw about the vertical axis, allowing for increased directional stability. Linking

rudder movement to tail wheel movement will allow for steering during taxi, takeoff, and landing using only one servo.

### 4.1.3 Propulsion Critical Parameters

### 4.1.3.1 Motor

Motors were analyzed based on several factors, primarily their static thrust capacity and their efficiency. A high static thrust

capacity is essential for generating enough thrust to fly with heavier payload weights. High efficiency is necessary to ensure the

aircraft can fly for as many laps as possible while maintaining high speeds, ensuring that the battery capacity is properly utilized.

Additionally, the motor must meet constraints placed by the AIAA rules for the competition.

### 4.1.3.2 Main Battery

The team considered a number of batteries that fell within the set of AIAA restrictions, with the goal of choosing a battery that

would provide sufficient power to the motor for propulsion. The battery’s capacity and performance are impacted by a number of

factors, which are analyzed in greater detail in Section 4.2.7.

### 4.1.3.3 Electronic Speed Controller

The ESC is essential for controlling the flow of power from the battery to the motor, as well as facilitating pilot input to control the

speed of the motor. To achieve this, it must be able to handle the battery’s maximum output current without taking up excessive

space or weight in the fuselage. Additionally, the team uses the ESC to collect experimental data during test flights in order to

better inform further design choices.

### 4.1.4 Flight Course Breakdown

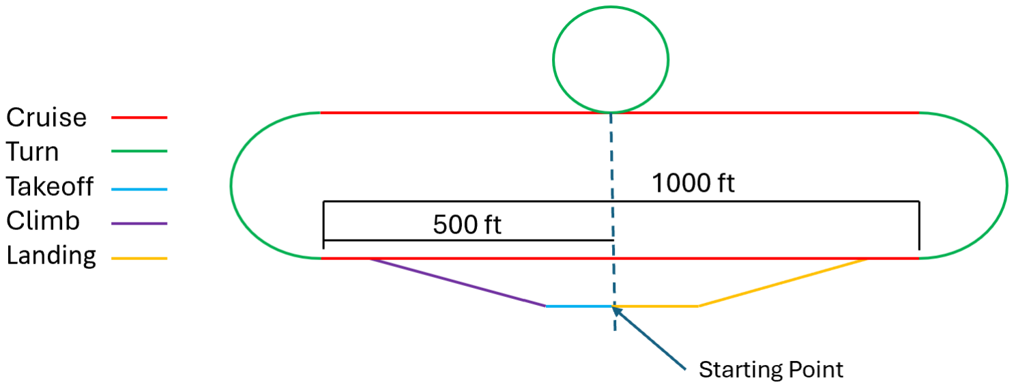
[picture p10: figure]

Figure 9: AIAA Standard Lap Components

### 4.1.4.1 Takeoff

Since the competition has no specified limit on takeoff distance, the only requirement the team considered was a maximum

distance of 250 feet, the distance of ND DBF’s testing runway.

University of Notre Dame | Page 18 of 60

### 4.1.4.2 Climb

Immediately after takeoff, a period of climb is required in order to fly at safe altitudes without obstruction or disturbances from the

ground, as well as to reach the required altitude for dropping the X-1 test vehicle in M3. For predictive purposes, the team will

model this period of climb using Equation (5), where Vclimb is the aircraft’s velocity, T is thrust, D is drag, and W is weight. In

this equation, the excess thrust is shown as (T − D), which produces the necessary force for the climb.

Rate of Climb =

Vclimb(T − D)
W

(5)

### 4.1.4.3 Cruise

Given the 1,000 ft and 500 ft straightaways that make up a significant portion of the flight course, a comprehensive understanding

of the aircraft’s performance at cruise is necessary to ensure accurate predictions and optimal mission performance. A detailed

analysis of cruise performance is discussed in Section 4.4.3. It should be noted that the team’s practical findings, discussed in

Section 3.2, indicate that cruise speed is not necessarily indicative of flight speed during a competition lap.

### 4.1.4.4 Turn

Faster flight times rely heavily on quick turns with short turn radii, which are directly affected by factors such as aileron effective-

ness and wing loading. These factors are analyzed in Section 4.4.4 to gain accurate predictions for performance across all flight

missions.

### 4.1.4.5 Landing

Given the high payload weights involved in this year’s design, ensuring a safe landing was of particular concern this year for

scoring points in any mission. The team went through a number of design changes to improve the aircraft’s ability to land safely;

these considerations are outlined primarily in Section 4.4.5.

### 4.1.5 Assumptions & Uncertainties

The design process of ND DBF featured two separate types of uncertainties, analytical and environmental. Analytical uncertain-

ties stem from standard mathematical models for aircraft not applying exactly to the aircraft as built. These can be caused by

differences in the final manufactured product when compared to the model analyzed in XFLR5 or OpenVSP, or by equations and

rules of thumb meant for full size aircraft design failing to translate on the scale of ND DBF’s work. These errors can be accounted

for by designing to a large factor of safety. Environmental uncertainties are presented in Table 14. These are the differences in

weather between the competition site in April and ND DBF’s testing site and season.

Table 14: Environmental Uncertainties
Uncertainty | Tucson International Modelplex Park Association | South Bend Radio Control Club, Bremen IN
Season | Spring | Late Fall/Winter/Early Spring
Average Temperature (High/Low/Mean) | 83°/52°/68° F | 44°/30°/36° F
Average Wind Speed | 12.7 ft/s | 17.3 ft/s
Elevation (above sea level) | 2,643 ft | 854 ft
Average Air Pressure | 2111 lbs/ft² | 2128 lbs/ft²
Air Density | 0.0023 slugs/ft³ | 0.0025 slugs/ft³

ND DBF’s testing site in Bremen, Indiana has several clear environmental differences when compared to the fly-off site in Tucson.

Firstly, because the air in Bremen is slightly denser than that in Tuscon, the lift generated by the aircraft will be slightly higher

University of Notre Dame | Page 19 of 60

during test flights. However, this difference in humidity creates differences in lift on a magnitude of less than Additionally, the fly-off

site is significantly hotter which could potentially lead to overheating of electrical components, such as the ESC, that would not be

experienced in the Bremen winter and early spring. To combat this, the team should add additional airflow to those components,

or use components rated well beyond the expected current draw of the system.

### 4.2 Design and Sizing Considerations

The following section describes the methodology and techniques used to translate conceptual and preliminary designs into

the qualitative and quantitative design parameters that define the detailed design. Sizes of lifting and control surfaces were

initially estimated using the aerodynamic equations outlined in the following sections. The team then verified and adjusted these

parameters through analyses using MATLAB programs [2] and the XFLR5 analysis software. XFLR5 determines coefficients of

lift, drag, and other aerodynamic parameters for different lifting surfaces and mass placements through Vortex Lattice Method [4].

XFLR5 is limited due to its inability to accurately simulate fuselage geometry, so further calculations were made using OpenVSP

[5], primarily to gain estimates of parasite drag in Section 4.4.1.

### 4.2.1 Wing Geometry

Because the wing is the primary source of lift, the team optimized its design parameters to maximize mission scoring. As detailed

in Section 3.2, the wing was preliminarily sized in the scoring analysis simulation script. This section details the most important

parameters that were considered to reach the preliminary wing geometry. The span was first set to 6 ft, the highest span allowed

by AIAA, to maximize aspect ratio for potential wing areas and maximize efficiency through the wing lift-to-drag ratio. This allows

for optimal trade-off between cruise speed and payload capacity. Scoring analysis script set the initial wing area at 3.85 square

feet, resulting in a mean aerodynamic chord of 9.43 in. A taper ratio of 0.6, optimized to minimize profile drag without over-sizing

the root chord, was applied to the wing to mitigate induced drag and further optimize the wing’s lift-to-drag ratio.

The slope for the 3D lift coefficient was calculated using Equation (6), where β is a function of the effective Mach number. Using

the predicted flight speed for the configuration, aircraft weight, zero lift angle of attack, and dCL
dα , the aircraft trim angle for steady,

level flight could be determined using Equation (4) stated in Section 3.2.

dCL
dα =

2πAR
2 + r
4 + (ARβ)

2

1 + tan²(Λt/c)
β²

(6)

After multiple test flights, the team determined that the aircraft’s glide slope was too steep for a safe landing, resulting in crashes

on landing. The wing geometry was reevaluated, as the team found that higher lift was required for softer landings. The aircraft’s

stall speed, the minimum speed required to maintain level flight, was calculated and used as a relative estimate of the aircraft’s

landing speed, as discussed in Section 4.4.5. Using these stall speed calculations, a wing area was calculated taking into account

the team’s goal for the total plane weight. To maximize the aspect ratio, the new wingspan was set to 64 in to allow for space at

the wingtips to fit the fuel tanks within the 6 ft limit. To improve roll stability, the team implemented a dihedral angle of 5 degrees,

as discussed in Section 4.3.2. The team determined basic metrics for the aircraft’s performance with the new wing, which are

listed in Table 15 using the selected airfoil geometries detailed in Section 4.2.4. These were used for further analysis on the new

wing geometry, which was conducted using XFLR5 to determine flight and stability characteristics in Section 4.4. As discussed

in Section 3.2, these cruise characteristics are not necessarily the average flight speed of the aircraft in a competition lap.

University of Notre Dame | Page 20 of 60

Table 15: Cruise Characteristics for All 3 Missions

### 4.2.2 Fuselage Design and Sizing

The implementation of a boom tail meant that minimizing fuselage length would also minimize overall drag, since a larger portion

of the aircraft would have lower surface area and therefore produce less surface drag. As such, the cross-sectional shape of

the fuselage needed to allow for the dense placement of components into a relatively short length of the fuselage, leading the

team to lean towards a rectangular cross-section that maximized internal area relative to the mostly rectangular components

being used (such as the battery and ESC). However, the shape of the fuselage’s cross-section also played a significant role in

drag minimization, favoring a more circular shape with rounded edges. To balance these requirements, the team chose to use

a Norman window cross-section for the fuselage, tapered at both ends and sized to incorporate all components with optimal

locations to achieve an ideal center of gravity.

### 4.2.3 Tail Design and Sizing

Through the trade study found in Section 3.3.3, the team settled on a conventional design for the overall configuration of the

vertical and horizontal stabilizers. The team chose to implement a symmetrical NACA 0012 airfoil for both the vertical and

horizontal stabilizers due to its high lift-to-drag ratio relative to other symmetrical airfoils as well as its reliability in previous years

as a tail airfoil. When sizing the tail, the team began by using a combination of tail sizing equations and conventional assumptions

to provide an initial estimate for sufficient tail sizing parameters. Volume coefficients for the horizontal and vertical tails (VHT

and VV T ) were determined to be 0.5 and 0.075, respectively, with the vertical tail’s coefficient being increased marginally from

the recommended 0.06 due to prior experience [6] . Using these, along with the main wing’s chord c¯W , area SW , and span

bW , the team utilized Equations (7) through (12) to determine appropriate ranges for the tail areas, SHT and SV T , as well as

the distances from the wing, lHT and lV T . Additional assumptions, made from previous experience and verified through listed

sources, were that the aspect ratio of the horizontal tail, ARHT , should be around half that of the wing, and the vertical tail’s

aspect ratio ARV T should be around 150% that of the wing [7]. Additionally, the taper ratio λ was set to 0.6 to minimize induced

drag and maximize structural efficiency. The tip chord of the vertical tail is offset in order to maintain a constant trailing edge.

VHT =

lHT SHT
c¯W SW
(7) VV T =

lV T SV T
c¯W SW

(8)

ARHT =

bHT

cHT

(9) ARV T =

b

2
V T
SV T

(10)

ARV T =

2bV T

cr,V T (1 + λV T )

(11) λ =

ct
cr

(12)

With these sizing estimates in mind, the team simulated tail designs | Table 16: Empennage Design Parameters

in XFLR5 to find a tail that provided proper stability in relation to the

predetermined wings and the constraints on component placements

within the fuselage. This process was used iteratively throughout

the year in response to necessary changes in the wing. Detailed

parameters for the tail design are found in Table 16.

University of Notre Dame | Page 21 of 60

### 4.2.4 Airfoil Design and Sizing

Aerodynamic design and analysis began with the airfoil selection for the main wing. The Airfoil Tools database [8] and XFLR5

were used to analyze airfoil characteristics of potential airfoils at the cruise Reynolds number, computed using Equation (13).

Re =

ρuc¯W
µ

(13)

With a 16.75 in chord, and an estimated cruise velocity of 77 ft/s, the Reynolds number was computed to be 700,000. Using

this Reynolds number, the team looked to narrow down the list of potential airfoils. Airfoils with both a high coefficient of lift and

high lift-to-drag ratio were prioritized to maximize payload weight and maximum cruise speed, respectively. Furthermore, only

airfoils with flat bottoms or symmetric geometries were considered in order to ensure ease of manufacturing. After analyzing the

database, referring to previous experiences, and discussing with technical advisors and prior DBF members, the team narrowed

its airfoil options to the three shown in Table 17.

Table 17: Airfoil Comparison

From Table 17, the Clark-Y and N-22 airfoils have a higher lift-to-drag ratio than the NACA 2213 airfoil, allowing for a faster cruise

speed. Between the Clark-Y and N-22, the N-22 has a higher maximum coefficient of lift and cruise coefficient of lift, as well as

a lower coefficient of drag at the maximum coefficient of lift. The N-22 was selected as the main wing airfoil to optimize payload

capacity and cruise speed.

### 4.2.5 Control Surface Design and Sizing

### 4.2.5.1 Elevator

The elevator was sized to trim the aircraft to a miminal angle of

attack using pitching moment data from XFLR5 as well as other

geometric parameters. Equations (14) and (15) below display

the process for computing the flap effectiveness parameter τ :

Cm = Cmo + (Cm,α)α + (Cm,δe

)δe = 0 | (14)

τ =

−(Cm,δe

)

ηHT VHT (CL,αHT )

| (15)

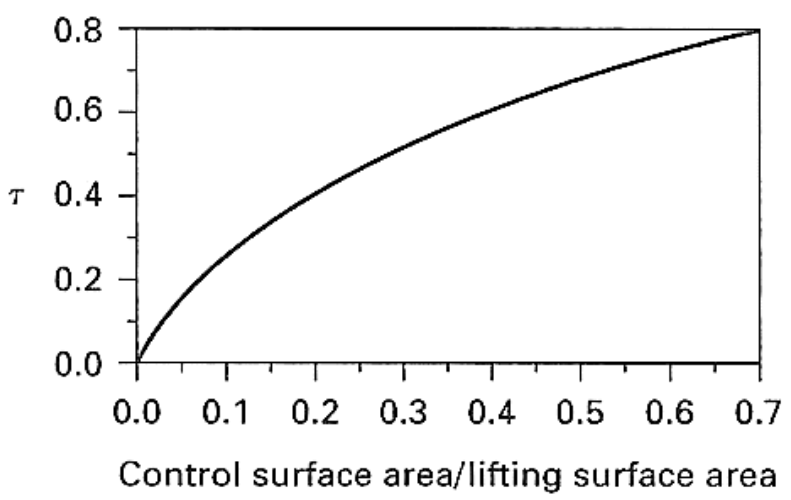
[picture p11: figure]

Figure 10: Flap Effectiveness Parameter, τ [9]

where Cmo is the zero angle of attack pitching moment coefficient, Cm,δe

is the slope of the Cm vs δe curve, δe is the elevator

deflection angle, ηHT is the horizontal tail efficiency, and CL,αHT is the slope of CL vs αHT curve. After computing τ , the

control surface area to lifting surface area ratio could be determined from Figure 10 above. From this, the elevator area could be

determined, yielding the dimensions found below in Table 18.

University of Notre Dame | Page 22 of 60

Table 18: Elevator Sizing Parameters

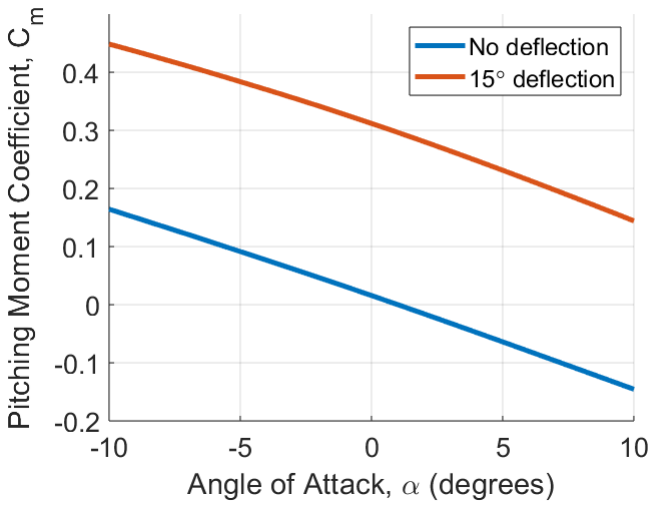
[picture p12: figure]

Figure 11: Pitching Moment Coefficient vs Angle of Attack

The actual as-built elevator was designed to be

able to exceed a 15 degree deflection angle to

provide more authority if necessary to account for

any inefficiencies due to manufacturing processes.

The elevator was implemented into the XFLR5 air-

craft model and Figure 11 was generated, further

demonstrating the ability of the elevator to trim the

aircraft to high angles of attack. Finally, flight test-

ing played a large role in finalizing the size of the

elevator. The team’s initial sizing decisions were

confirmed after receiving positive feedback affirm-

ing the elevator’s sufficient control authority from the

team’s pilot.

### 4.2.5.2 Rudder

The rudder was sized for the aircraft to trim a 20 ft/s crosswind using yawing moment data from XFLR5 as well as other geometric

parameters. Equations (16) and (17) below display the process for computing the flap effectiveness parameter τ :

Cn = Cno + (Cn,β)β + (Cn,δr

)δr | (16)

τ =

−(Cn,δr

)

ηV T VV T (CL,αV T )

(17)

where Cn is the yawing moment coefficient, Cno is the zero angle of attack yawing moment coefficient, Cn,β is the slope of the

Cn vs β curve, Cn,δr

is the slope of the Cn vs δr curve, δr is the rudder deflection angle, ηV T is vertical tail efficiency, and

CL,αV T is the slope of the CL vs αV T curve. After computing τ , the control surface area to lifting surface area ratio could be

determined from Figure 10 above. From this, the rudder area could be determined, yielding the dimensions found in Table 19.

Table 19: Rudder Sizing Parameters

University of Notre Dame | Page 23 of 60

Figure 12: Yawing Moment Coefficient vs Sideslip Angle

Like the elevator, the actual as-built rudder was de-

signed to be able to exceed a 15 degree deflec-

tion angle to provide more authority if necessary

to account for any inefficiencies due to manufactur-

ing processes. The rudder was implemented into

the XFLR5 aircraft model and Figure 12 was gener-

ated, further demonstrating the ability of the rudder

to trim the aircraft during side slipping. As before,

flight testing played a large role in finalizing the size

of the rudder. After testing the design in flight, the

team also confirmed with the pilot that this rudder

sizing provided effective control.

### 4.2.5.3 Ailerons

The ailerons were sized to provide adequate roll authority for the aircraft using rolling moment data from XFLR5 as well as other

geometric parameters. Equations (18) and (19) below display the process for computing the flap effectiveness parameter τ :

Cl = (Cl,β)β + (Cl,δa

)δa | (18) | τ =

bW (Cl,δa

)

2(CL,αW )

(19)

where Cl

is the roll moment coefficient, Cl,β is the slope of the Cl vs β curve, Cl,δa is the slope of the Cl vs δa curve, δa is

the aileron deflection angle, and CL,αW is the slope of the CL vs αW curve. After computing τ , the control surface area to

lifting surface area ratio could be determined from Figure 10 above. From this, the aileron area could be determined, yielding the

dimensions found below in Table 20.

Table 20: Aileron Sizing Parameters

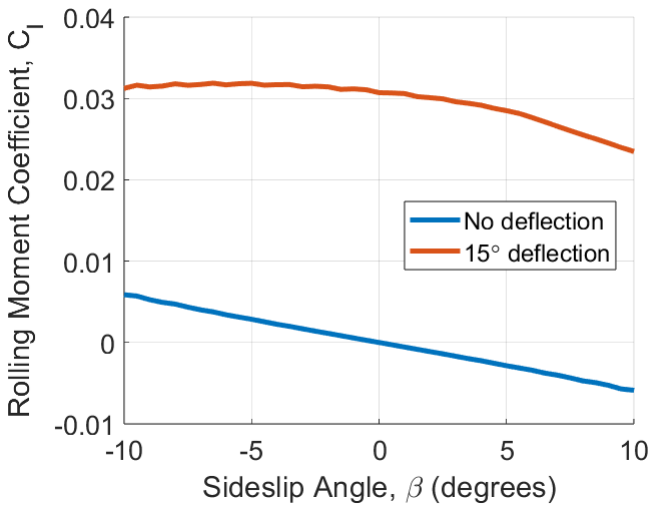
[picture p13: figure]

Figure 13: Rolling Moment Coefficient vs Angle of Attack

The actual as-built ailerons were designed to be

able to exceed a 15 degree deflection angle to pro-

vide more roll authority if necessary to account for

any inefficiencies due to manufacturing processes.

The ailerons were implemented into the XFLR5 air-

craft model and Figure 13 was generated, further

demonstrating the roll authority generated by the

ailerons. As with the other control surfaces, flight

testing played a large role in finalizing the size of

the ailerons, and the team used pilot feedback from

test flights to confirm that the ailerons provided suf-

ficient roll authority.

University of Notre Dame | Page 24 of 60

### 4.2.6 Servo Torque Sizing

The team calculated the torque required to fully actuate each control surface from an online RC Airplane Torque Calculator [10].

Table 21 details the required and recommended torque for each control surface. The recommended torque is calculated using a

safety factor of 1.3.

Table 21: Servo Torque Requirements for Each Control Surface

The team elected to use KST X10 Mini Digital Servos which provide 94 oz-in of torque because of their small form factor and

large torque capacity. Although the maximum recommended torque is nearly reached on the ailerons, the factor of safety remains

1.1 above the required torque, which was deemed adequate for Mk 1.

### 4.2.7 Propulsion Design and Sizing

The team used the scoring optimization analysis performed at the beginning of the year to design the propulsion system. In this

analysis, the team analyzed motor and propeller configuration performance data charts provided by the manufacturers such as

BadAss [11], Cobra [12], and Tempest [13]. A range of battery manufacturers was also analyzed from brands such as Liperior

[14] and MaxAmps [15]. These brands were selected because of their high-quality ratings, easily accessible data charts, and

diversity of motor and battery size. The performance charts were key pieces of information used to determine the propulsion

design, including static thrust, current draw, RPM, and optimal propeller size. As outlined in Section 3.2, a prospective propulsion

configuration must meet several baseline requirements. First, a motor/propeller that provides a minimum thrust-to-weight ratio

of 1.2 must be found on the performance data sheets. This value was selected from previous team DBF experience, advice

from experienced RC pilots, and the knowledge that one must produce extra thrust to counteract the drag from the payload

bottles. Second, an available battery must have enough power to allow 5.5 minutes of continuous flight. This was calculated

using Equation (21). Third, a motor/propeller configuration must provide enough static thrust to enable the aircraft to take off in

less than the length of the team’s testing runway, 250 ft. These calculations are covered in more detail in Section 4.4.2.

This detailed analysis provided the team with multiple high-scoring propulsion configurations for the aircraft design. The team

then purchased one motor that met the team’s budget requirements and multiple propellers for further testing. More detailed

theoretical analysis of dynamic thrust was completed on each propeller using data provided by Advanced Precision Composites

(APC) [16] provided data and calculated using blade element theory [3]. Given that the maximum RPM of the motor is roughly

7000 RPM’s, dynamic thrust values from a propellor of the same diameter and pitch as the one selected by the scoring analysis

code were selected from the APC data base, and plotted with velocity. This data is further described in Section 4.4.3. The

components selected during the perliminary design stage are summarized in Table 22.

T
W

≥ 1.2 =

Maximum Motor Static Thrust Aircraft Mission Weight

(20)

Flight Time =

Battery Amp Hours × 60
0.85 × Motor Static Current Draw

(21)

University of Notre Dame | Page 25 of 60

Table 22: Detailed Propulsion Design

Motor | ESC | Battery | Propellor
Badass 6245 180kV | Phoenix Edge HVF 160 | MaxAmps 12S 2250mAh Li-Po | Badass 20x12

### 4.3 Stability and Control

### 4.3.1 Static Stability

The team began stability and control analyses by determining the aircraft’s static margin, as defined in Equation (22). This varied

slightly between missions for the unloaded aircraft in M1, the aircraft loaded with fuel tanks in M2, and the aircraft loaded with

the x-1 test vehicle in M3. The team determined about 20% to be an ideal static margin based on past designs and conventional

stability assumptions for RC aircraft of this scale. Table 23 displays the static margin for each mission, which all remain within 2%

of the goal of 20%.

SM =

XNP − XCG
c¯W

(22)

Table 23: Static Margin Parameters

To further ensure static stability, XFLR5 was used to generate values for the pitching moment coefficient, Cm, at various angles of

attack, and the yawing moment coefficient, Cn, at various sideslip angles. The negative Cm vs α slope indicates a slight forward

pitching tendency at low angles of attack with an intercept just over the origin at 0.017, indicating a statically stable aircraft with

the desired tendency to slightly pitch forward. This is particularly important for preventing stalling at high critical angles of attack,

as the forward pitching moment naturally forces the aircraft back into safe angles of attack. The positive Cn vs β slope passing

through the origin indicates desired lateral stability. Slopes from these analyses yielded static stability derivatives, detailed in

Table 24.

Table 24: Lateral and Longitudinal Static Stability Derivatives

### 4.3.2 Dynamic Stability

After verifying static stability, the dynamic stability of the aircraft was analyzed in XFLR5 for all three missions. A crucial component

of designing for dynamic stability was the implementation of a dihedral wing angle of 5 degrees. With this design, a lateral rolling

disturbance results in a lift vector that offsets the disturbance, thereby increasing roll stability and dampening spiral divergence.

Figure 14 displays the root locus plots for the lateral and longitudinal dynamic stability modes.

University of Notre Dame | Page 26 of 60

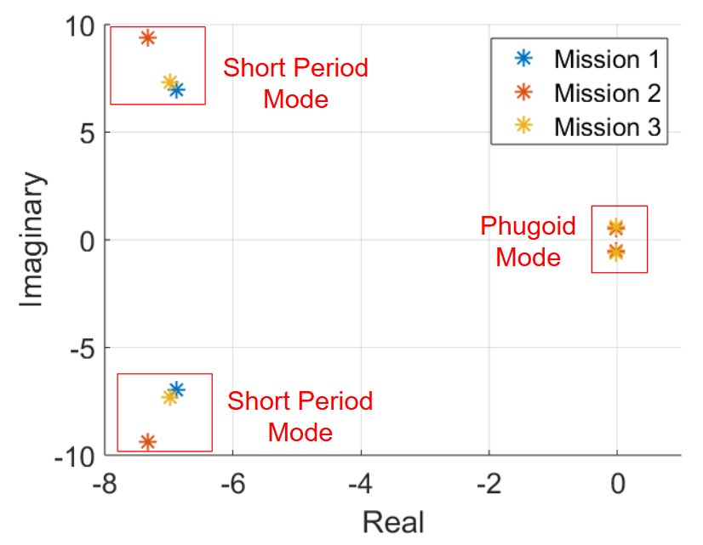
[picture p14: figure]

(a) Lateral Stability | (b) Longitudinal Stability

Figure 14: Root Locus Plots

The real part of each root determines the stability of its associated mode. A negative real part corresponds to a stable response,

whereas a positive real part corresponds to an unstable response. As seen in Figure 14, each mode has a negative real part

and thus a stable response except for the spiral mode, which has a slightly positive real part. This indicates a divergent spiral

mode; however, this is common in many aircraft and can be corrected with pilot input given a slow growth rate. The fastest time

to double for a spiral mode perturbation is over 19 seconds in M2. Flight tests have demonstrated that this is more than enough

time for the pilot to correct a spiral mode disturbance. Figures 15 and 16 depict time response analyses, performed in XFLR5, for

both longitudinal and lateral stability modes.

(a) Phugoid | (b) Short Period

Figure 15: Time response plots for longitudinal stability modes.

University of Notre Dame | Page 27 of 60
(a) Roll | (b) Dutch Roll
(c) Spiral Divergence

Figure 16: Time response plots for lateral stability modes.

Each of these plots display sound dynamic stability according to Sadraey [6]. The damping in the phugoid mode, which halves in

roughly 10-15 seconds for each mission, is within the standard time to half for phugoid mode of 30-120 seconds [3]. Short period

and dutch roll modes also decay rapidly, and for this reason, will not cause controllability issues. The roll response, although an

unstable mode, takes 20 seconds in M2 to double, which is more than enough time for the pilot to react and correct for the spiral

mode, as shown in Table 25.

Table 25: Dynamic Stability Analysis for All 3 Missions

(a) Times to half/double for longitudinal and lateral modes. | (b) Dynamic stability derivatives for longitudinal and lateral modes.

University of Notre Dame | Page 28 of 60

### 4.4 Performance Analysis

### 4.4.1 Lift and Drag

The team utilized XFLR5 to gain accurate representations of the lift and drag forces, outlined in Figures 17a and 17b. Local

values of CL are plotted across the span of the wing and horizontal stabilizer in Figure 17a, and total values of CL are plotted

over various angles of attack α in Figure 17b. The y-intercept of this plot indicates a positive CL of 0.29 at a 0° angle of attack,

which increases by 0.07 for each degree increase in α.

(a) Spanwise Lift Distribution on Aircraft at Zero Angle of Attack | (b) 3D CL vs α Curve for Main Wing

Figure 17: Primary Aerodynamic Characteristics of Aircraft

ND DBF used the OpenVSP [5] parasite drag analysis tool to calculate the total parasite drag of the aircraft. The tool uses linear

inviscid models to calculate the parasite drag of each component. The induced drag CDi was calculated from the aspect ratio,

AR, Oswald efficiency factor, e, and the coefficient of lift, CL, in cruise, shown in Equation (23) below.

CDi =

CL
πeAR | (23)

Figures 18 and 19 illustrates the force of drag calculated for each component and total drag force sum above each bar. These

values were obtained using Equation (24) below, where ρ is air density, V is velocity, and SW is cross sectional area.

D =

1
2
ρV ²CDSW | (24)

The components which contributed most to the overall drag were the main wing, with the largest wetted area, the horizontal tail,

with the second largest wetted area, and the landing gear, with the highest form factor. As expected, the induced drag is highest

for M2, where the total aircraft weight is the highest.

University of Notre Dame | Page 29 of 60

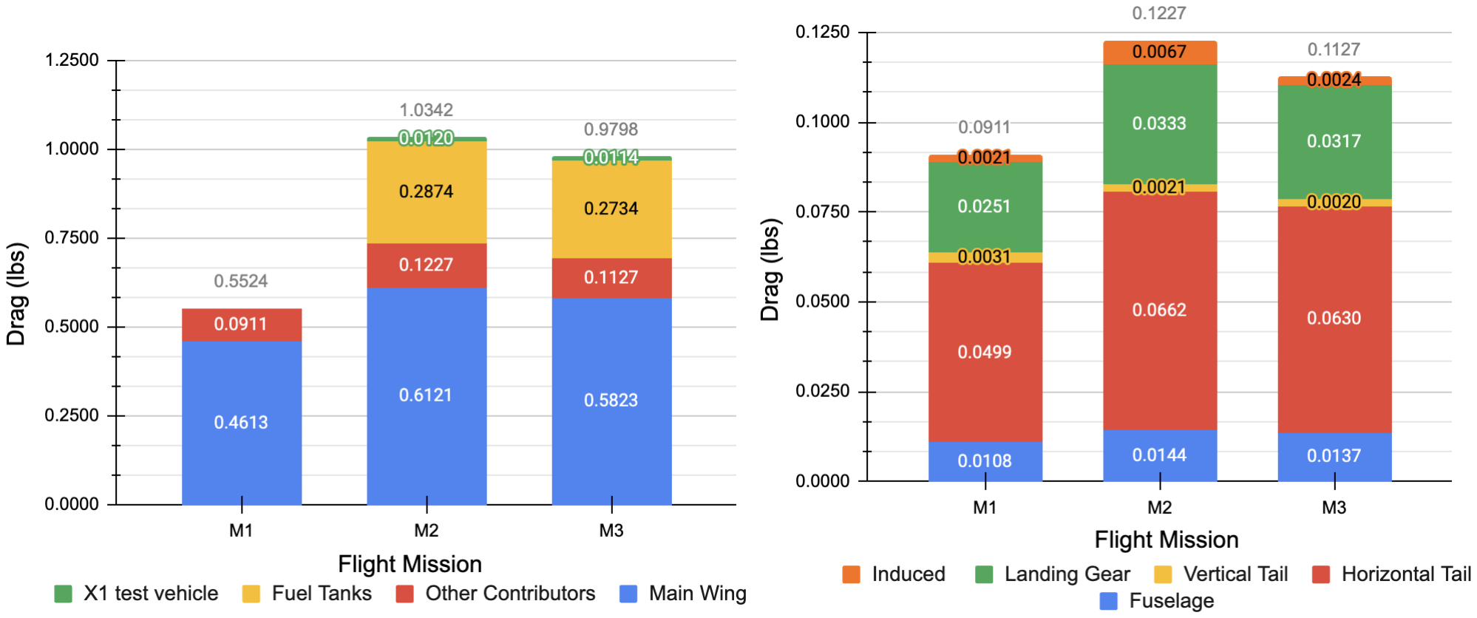
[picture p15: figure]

Figure 18: Aircraft Wing Drags for Each Flight Mission | Figure 19: Aircraft Component Drags for Each Flight Mission

### 4.4.2 Takeoff Distance

To ensure the aircraft could takeoff within the length of

the testing runway, a fourth order Runge-Kutta (RK4)

simulation was implemented. This program increments

through time until the aircraft achieves enough lift for

takeoff. Figure 20 illustrates the takeoff runs for M1, M2,

and M3, respectively. Each line’s termination point rep-

resents the position and time at which the aircraft gener-

ates enough lift to takeoff. As can be seen, the aircraft

takes off in both loaded and unloaded cases without any

gusts or flaps implemented.

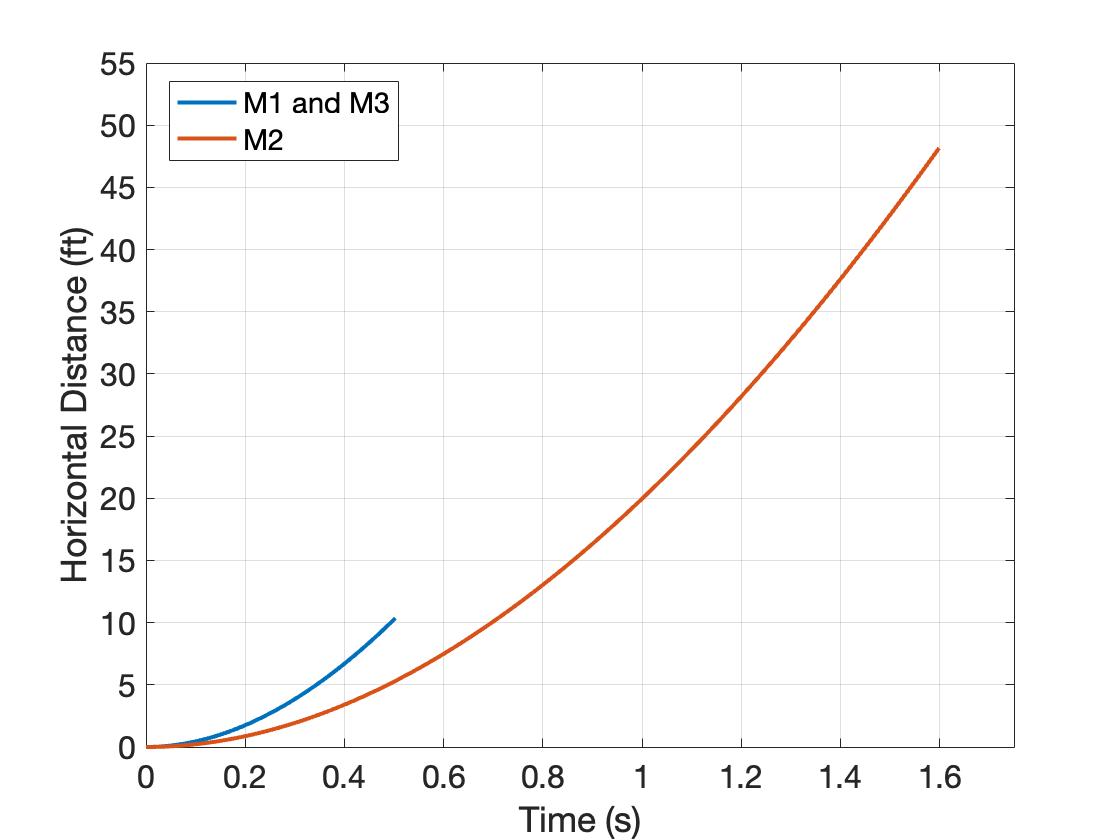
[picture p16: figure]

Figure 20: Takeoff Runs for Multiple Missions

### 4.4.3 Maximum Cruise Velocity

The maximum cruise speed for each mission significantly influences the mission score. The team found this speed by identifying

the intersection point of the dynamic thrust and thrust required curves, as discussed in previous sections (4.4.1 for drag or thrust

required). Figures 21, 22, and 23 visually represent the excess thrust at various velocities throughout each mission, as well as

the terminal cruising velocity where the two curves intersect.

University of Notre Dame | Page 30 of 60

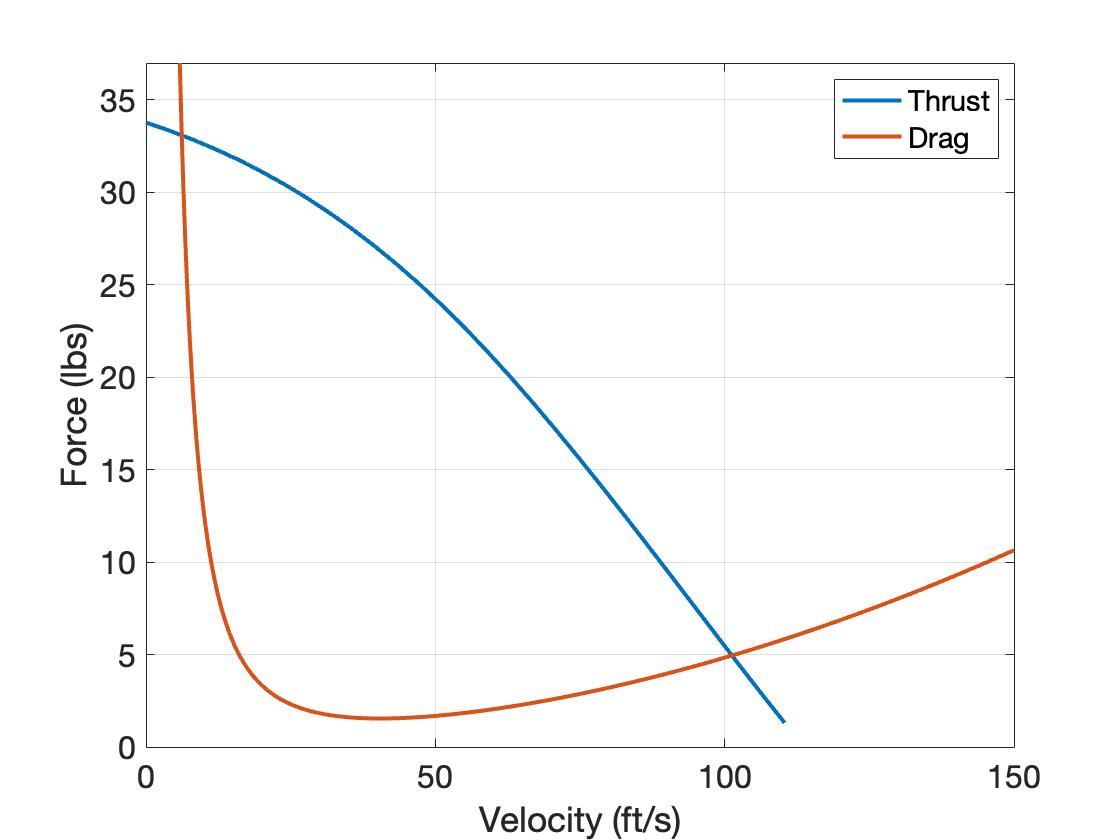
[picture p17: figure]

Figure 21: M1 Excess Thrust | Figure 22: M2 Excess Thrust

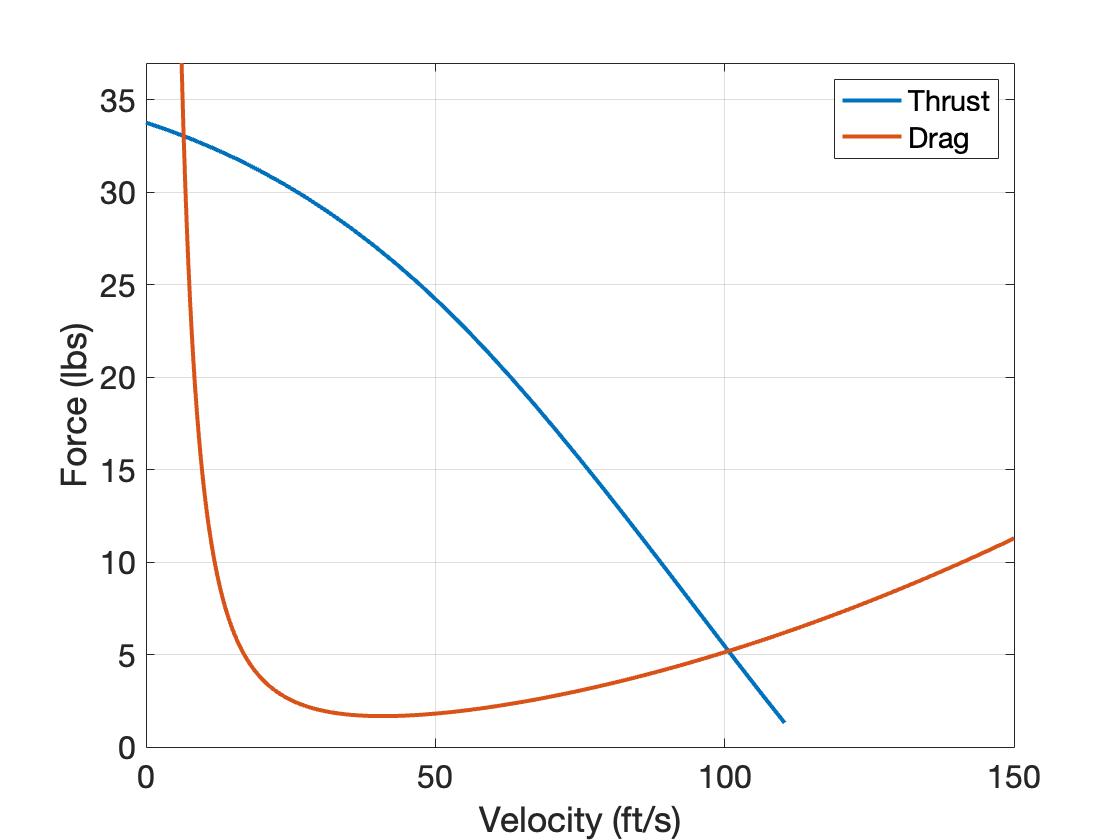
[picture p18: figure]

Figure 23: M3 Excess Thrust

The dynamic thrust in these figures corresponds to a 20x12 propeller spinning at 7000 RPM. The drag curve represents the

combined parasite and induced drag for the mission. Table 4 in Section 3.2 lists the exact maximum flight speed for each mission.

While these speeds are all similar, M2 flight speed is the lowest, as expected due to the higher payload weight in this mission.

### 4.4.4 Turning Analysis

The aircraft’s level turning performance is limited by structural and aerodynamic design, as well as available power. The limiting

load factor determines the maximum bank angle that the vehicle can maintain in level flight without exceeding the airplane’s

structural limitations or stalling. Equations (25) and (26) were used to approximate turn radius in a sustained turn, which would

produce the highest load.

University of Notre Dame | Page 31 of 60

n =

### vuut

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
q · CD0

W
S

!
(25)

ψ˙ =

g

√
n² − 1
V

=

V
R

(26)

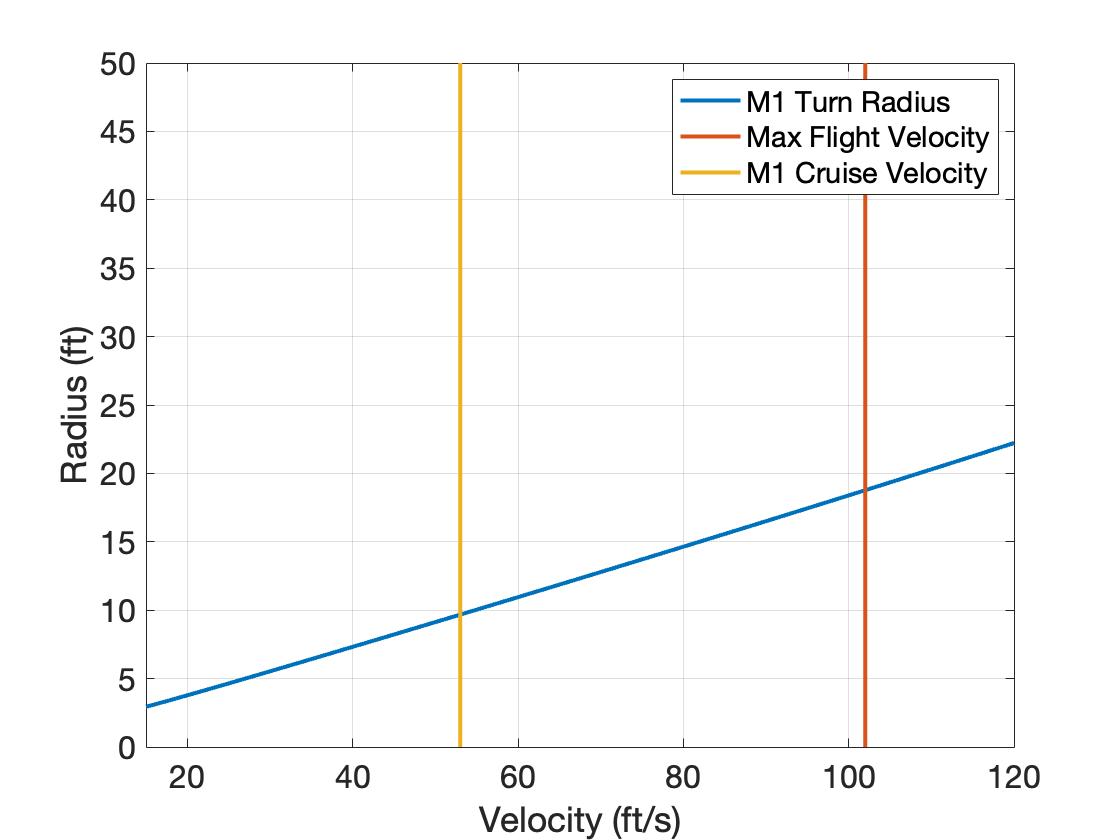
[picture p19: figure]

Figure 24: M1 Turn Radius as a Function of Turn Velocity

In these equation, V is the turn velocity, R is the turn radius, W
S

is wing loading, T
W is thrust-to-weight ratio, q is dynamic pressure, k is 1 πeAR , CD0 is the base coefficient of drag, and ψ˙
is the turn rate in radians per second. Figures 24, 25, and 26 illustrate the

turn radius as a function of velocity. For each mission the cruise speed and maximum speed are plotted, revealing a turn radius

of about 19 ft in M1, 37 ft in M2, and 20 ft in M3, if the aircraft maintains top speed throughout the turn.

Figure 25: M2 Turn Radius as a Function of Turn Velocity | Figure 26: M3 Turn Radius as a Function of Turn Velocity

### 4.4.5 Landing Speed

As mentioned in Section 4.2.1, the team used stall speed calculations to comparatively estimate the aircraft’s landing speed. The

stall speed VS was found using Equation (27), where W is the total aircraft weight, ρ is air density, SW is the wing area, and

CLmax
is the maximum coefficient of lift for the N-22 airfoil at Reynolds numbers of up to 500,000 [17]. This value was compared

to stall speeds of previous aircrafts and found to be significantly higher; using previous aircrafts and pilot input as a guide, the

team determined a safe region of stall speeds to be under 40 ft/s. With these parameters, the team determined approximate

wing areas in relation to total aircraft weights. Based on historical precedents concerning structural and manufacturing issues,

the team chose to cap the maximum wing area at 7.5 square feet to ensure a feasible design. This area correlated with a total

plane weight of 18.5 pounds.

Vs =

s
2W

ρSW CLmax

, | (27)

University of Notre Dame | Page 32 of 60

### 4.5 Overall Predicted Mission Performance

The team derived estimates for the aircraft’s overall performance from the conceptual design outlined above. These parameters

were found using XFLR5 alongside previously mentioned aerodynamic equations computed using MATLAB scripts. These factors

were mainly dependent on the wing area, 1072 in²
, the rectangular planform with 0-degree sweep and incidence angles, the wing

aspect ratio of 3.82, and the mean aerodynamic chord of 16.75 in. Calculated values for these performance parameters are

outlined in Table 26.

Table 26: Mission Performance Parameters

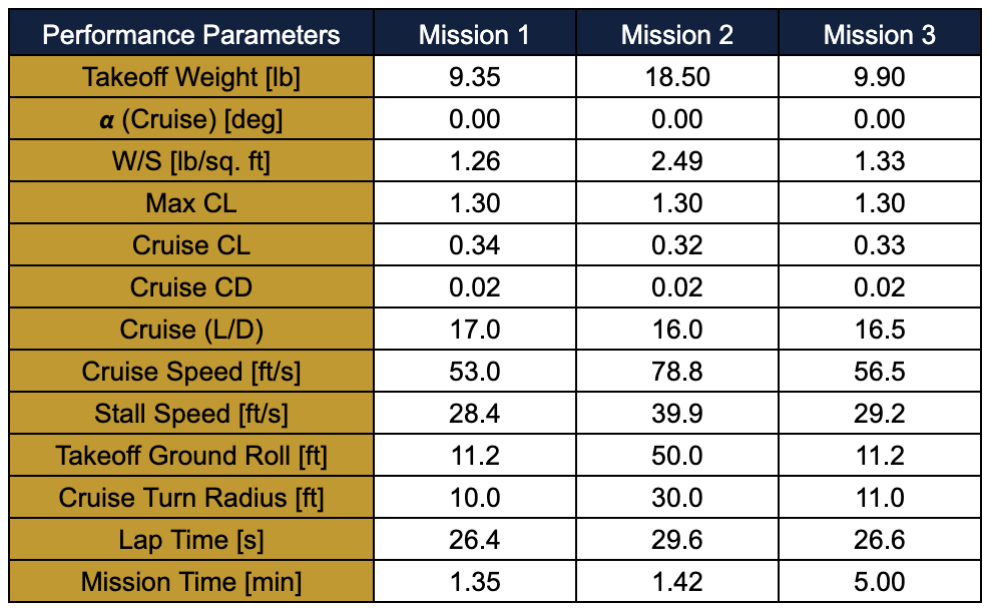
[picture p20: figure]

## 5 Detailed Design

The team conducted multiple design iterations in the conceptual and preliminary design phases. Subsystems saw changes

between every iteration to optimize performance, decrease weight, and increase efficiency. Table 27 shows the dimensions and

specifications of all the competition aircraft’s main subsystems.

Table 27: Aircraft Dimensions and Component Specifications
Wing | Vertical Tail | Propulsion
Span | 64 in | Span | 12 in | Motor Model | BadAss 6245
Chord Length | 16.75 in | Tip Chord | 7 in | Motor KV | 180
Airfoil | N-22 | Root Chord | 10 in | Motor Weight | 2.42 lb
Aspect Ratio | 3.82 | Airfoil | NACA 0012 | Propeller | BA 20 x 12 Wood Electric
Static Margin | 19.06% | Weight | 0.25 lb | Propulsion Battery | MaxAmps 12s 2250mAH Li-Po
Weight | 0.984 lb per wing | Stabilizer Area | 102 sq. in | Battery Capacity | 2250 mah
Wing Area | 1072 sq. in | Aspect Ratio | 5.65 | Battery Weight | 1.440 lb
Horizontal Tail | | Fuselage | | Max Continuous Current | 67.5 A
Span | 30 in | Weight | 0.912 lb | ESC
Chord Length | 13 in | Total Length | 32.625 in | Model | Castle Creations Phoenix Edge HV 160
Airfoil | NACA 0012 | Boom Length | 25.12 in | Voltage Rating | 50.4 V
Weight | 0.6 lb | Cross Sectional Area | 17.284 sq. in | Max Continuous Current | 160 A
Stabilizer Area | 390 sq. in | | | Weight | 0.602 lb
Aspect Ratio | 2.31 | | | Controls
| | | | Transmitter | Spektrum iX12
| | | | Receiver | Spektrum AR8020T
| | | | Battery Weight | 0.194 lb
| | | | Servos | KST X10

University of Notre Dame | Page 33 of 60

### 5.1 Structural Characteristics and Capabilities

### 5.1.1 Structural Limits of Main Wing Spar

The maximum load factors experienced by the aircraft for each mission were computed using Equation (28), with a maximum

velocity, Vmax, of 95 ft/s, a maximum lift coefficient, CLmax
, of 1.19, and the total aircraft weight for each mission. These load

factors are shown in Table 28.

nmax =

Lmax
W

=

1/2 ρV ²
maxSW CLmax
W

(28)

nlimit =

2Mmax
lL²

(29)

Table 28: Maximum Load Factors

To ensure the spar could withstand these loads, the maximum structural load factor, nlimit, was calculated based on the maximum

moment, Mmax, on the spar (modeled as a cantilever beam) which was calculated using FEA. Equation (29) was used to

determine nlimit = 12.4.

### 5.1.2 Shear and Bending Analysis of Main Wing Spar

The maximum stress was calculated using Equation (30), with c being the distance from the neutral axis to the farthest point of

the spar’s cross-section. The value c was iterated over as different spar geometries were evaluated. I is the second moment of

inertia, which was calculated for the hollow spar geometry using Equation (31). The value r represents the outer spar radius and

r1 is the inner radius.

σ =

cMmax
I
(30) I =

2πr⁴
64

−

2πr⁴
1
64

(31)

The stress was then compared to the ultimate tensile strength of carbon fiber, which was estimated to be 500,000 psi from the

lowest value found [18]. A hollow circle cross section was output as optimal with a resulting safety factor of 2.35. Using the

calculated lift values on each wing rib, shear and moment diagrams were generated to act as visuals of how the wing load is

distributed across the spar and are displayed in Figure 27.

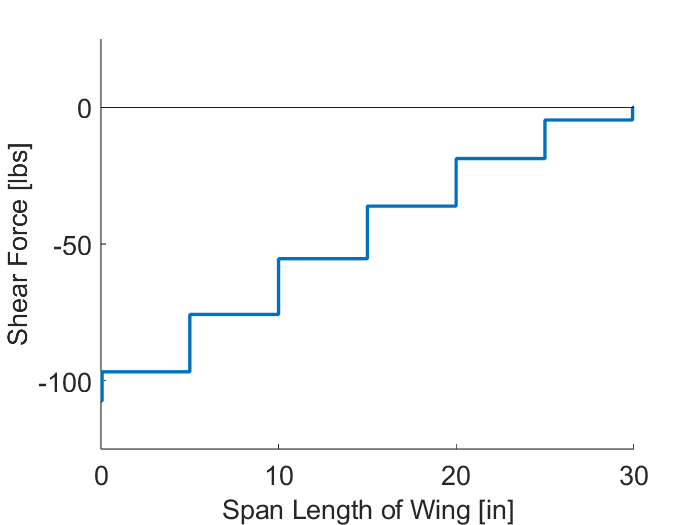
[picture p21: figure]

(a) Wing Spar Shear Diagram | (b) Wing Spar Moment Diagram

Figure 27: Shear and Moment Analysis of Spar During Maximum Loading

University of Notre Dame | Page 34 of 60

### 5.2 Subsystem Design

### 5.2.1 Fuselage Design

The fuselage is 32.5 in long with a Norman window cross section. The curved top was manufactured using balsa sheeting

to optimize aerodynamics and weight. The side panels, floor, and platforms in the fuselage are constructed from 0.125 in lite

plywood, which is stronger and less flexible than balsa. The fuselage is composed of three main compartments, with the front

two compartments containing two levels and top hatches, while the third is one level and accessible by side hatch. The last seven

inches of the fuselage tapers from a Norman window shape to the carbon-fiber boom tail. The front of the fuselage features a 3D

printed nose cone that houses the motor and minimizes drag. The back of the fuselage has a similar cone to transition between

the fuselage and boom tail.

### 5.2.2 X-1 Test Vehicle

### 5.2.2.1 Structural Design

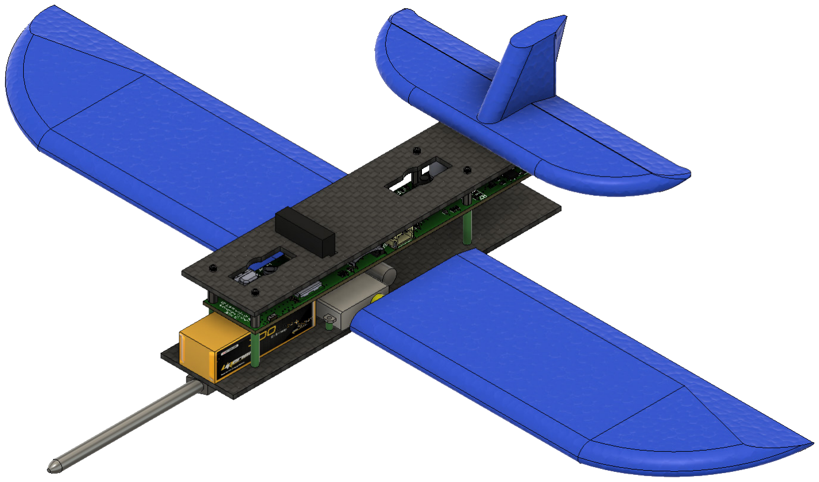
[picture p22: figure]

Figure 28: X-1 Test Vehicle CAD

The X-1 test vehicle, shown in Figure 28, is constructed using two

carbon fiber plates, the top being 5.9 in x 1.4 in x 0.079 in and the

bottom being 6.3 in x 1.4 in x 0.079 in. The plates are vertically

connected and separated by four 0.4375 in threaded hex stand-

offs, which are secured with 0.625 in head screws. Carbon fiber

was selected as the construction material of the vehicle because

of its superior durability and minimal weight, ensuring the vehicle

is able to safely reach the designated landing zone and withstand

landing impact. The top plate features two water jet-cut incisions for the release mechanism as well as a 1 in x 0.13 in horizontal

incision to allow for the attachment of a magnetic proximity sensor for release confirmation. The pitch and roll of the test vehicle

are controlled using two foam wings. A low wing was chosen to ensure the quarter inch clearance from the main aircraft wings.

These wings feature a semi-rectangular planform with lifted wingtips, actuated at the quarter cord by two X08H KST Servos. The

wings move symmetrically to control the pitch and asymmetrically to control the roll. The vehicle also includes a foam static hori-

zontal and vertical stabilizer to improve flight stability. The vehicle features a custom-made printed circuit board (PCB), designed

in Fusion and situated 0.598 in above the bottom plate for the autopilot system.

### 5.2.2.2 Printed Circuit Board Design

The PCB consists of an inertial measurement unit (BNO085), a GPS (NEO-M9N), and a differential pressure sensor (ABP2) to

gather rotational, groundspeed, and airspeed data, respectively. A magnet is mounted to the bottom of the fuselage so that a

magnetic proximity sensor connected to the PCB can be used to detect the release of the X-1 test vehicle. A proportional-integral-

derivative (PID) program was uploaded to the microcontroller that uses the sensors’ data to turn on the strobe lights after the

release, execute a 180 degree turn, and control rotational movement to autopilot the X-1 test vehicle to the 2.5-point bonus box.

An SD card was included on the PCB to gather data during testing to be used to optimize the PID program.

The ESP32 Pico V3 microcontroller was selected due to its lightweight package, dual-core processor, and 160 MHz CPU. The

package also has built-in flash memory and a crystal oscillator, reducing the area required for its peripherals. The PID program

takes advantage of the two cores and the CPU speed by integrating a real-time operating system (RTOS). This allows data to be

collected on one core and commands to be sent on another at a considerably high speed; this reduces latency and eliminates

University of Notre Dame | Page 35 of 60

any command blocking. Sensors send data to the ESP32 on an I2C bus, while an SD card logs the data on a separate SPI bus,

also to reduce latency and command blocking. The PCB can be powered by a 5-volt USB-C connection during programming or

by a two-cell LiPo battery during flight. A power multiplexor (TPS2121) selects the higher input voltage to power the board so that

switching between power sources is automatic. Regardless of the input voltage used, a buck converter (TPS62142) steps down

the input to 3.3V to power all sensors, the microcontroller, and data logging components. A 5V boost converter (MIC2875) steps

up 3.3V to 5V to power the addressable LEDs used as strobe lights. A secondary boost converter (TPS55340) steps up the input

to 8.4V to power the servos. Figure 29 shows the board layout and component grouping, and Table 29 describes the functions of

each major component. The board has four copper layers. The first and fourth layers are used for signal traces, the second layer

is used as the ground plane, and the third as a 3.3V plane since that is the most commonly used voltage on the board.

Table 29: Component Functions
Subsystem | Component | Function
Programming | CP2102 | Converts USB-UART serial communication from programming device (laptop) to ESP-32.
| ESP32-PICO-V3 | Microcontroller to collect and process data from sensors and control servos and LEDs.
Power | TPS2121 | Power Multiplexor that selects the power input between the USB and Battery to power the board.
| TPS62142 | Buck converter that steps down input voltage to 3.3V for all sensor and ESP32 logic/power.
| MIC2875 | Boost converter that steps up 3.3V to 5V for addressable LED (strobe light) logic/power.
| TPS55340 | Boost converter that steps up input voltage to 8.4V to power control surface servos.
| Liperior 2S 300mAh | Two cell LiPo that powers the board during the mission.
Data | BNO085 | Intertial Measurement Unit provides rotiational movement data.
| NEO-M9N | GPS provides location and groundspeed data.
| ABP2 | Differential pressure sensor that provides airspeed data when pitot tube is implemented.
| SD Card | Data logger for all sensor and control outputs.
Mission Compliance | WS2812B | Addressable LEDs used as strobe lights.
| LittelFuse 59140-030 | Magnetic proximity sensor used to detect release of the glider.
Flight Control | KST X08H | Servos used to actuate wings.

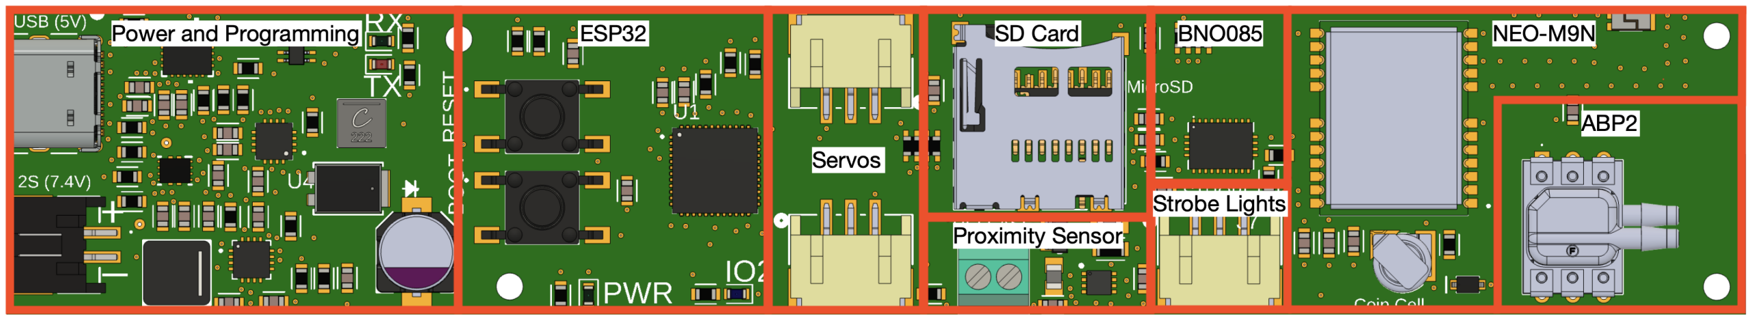
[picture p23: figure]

Figure 29: X-1 Test Vehicle Printed Circuit Board

The estimated current draw of the programming modules, sensors, LEDs, and servos is 1.3A; each power component has a

current rating of greater than 3A to provide sufficient margin. Similarly, the LiPo battery has a continuous discharge rating of

19.5A. The passive components, such as resistors and capacitors, are all sized at 0603 since they use a relatively small surface

area compared to all the active components, reducing the required board area and weight. Similarly, the GPS uses a ceramic

chip antenna to connect to satellites because it is surface-mounted with a small package size, eliminating the need for a heavy,

wired antenna. JST-PH connectors for the battery, servos, and strobe lights were selected, as they are sturdy enough to remain

plugged in during all stages of M2 and M3.

### 5.2.2.3 Control Software Design

The flight control software running on the ESP32 microcontroller uses FreeRTOS tasks to maximize system performance by

leveraging parallelism across both cores and is outlined in Figure 30. The system first performs an initialization routine that

involves verifying that each of the ESP32’s peripherals are functioning correctly. This includes the serial I/O, I2C bus for each

University of Notre Dame | Page 36 of 60

sensor (GPS, IMU, and airspeed), SD Card (SPI bus) data logging, strobe LED (initialized off), and both wing actuation servos.

Servo actuation tests confirm the servo range of travel and allow for verification of the servo trim settings necessary to maintain a

neutral (level wings) position. After initialization is complete, the microcontroller enters light sleep and suspends both CPUs until

a high to low transition is detected on GPIO pin 4 to which the magnetic release detection sensor is attached.

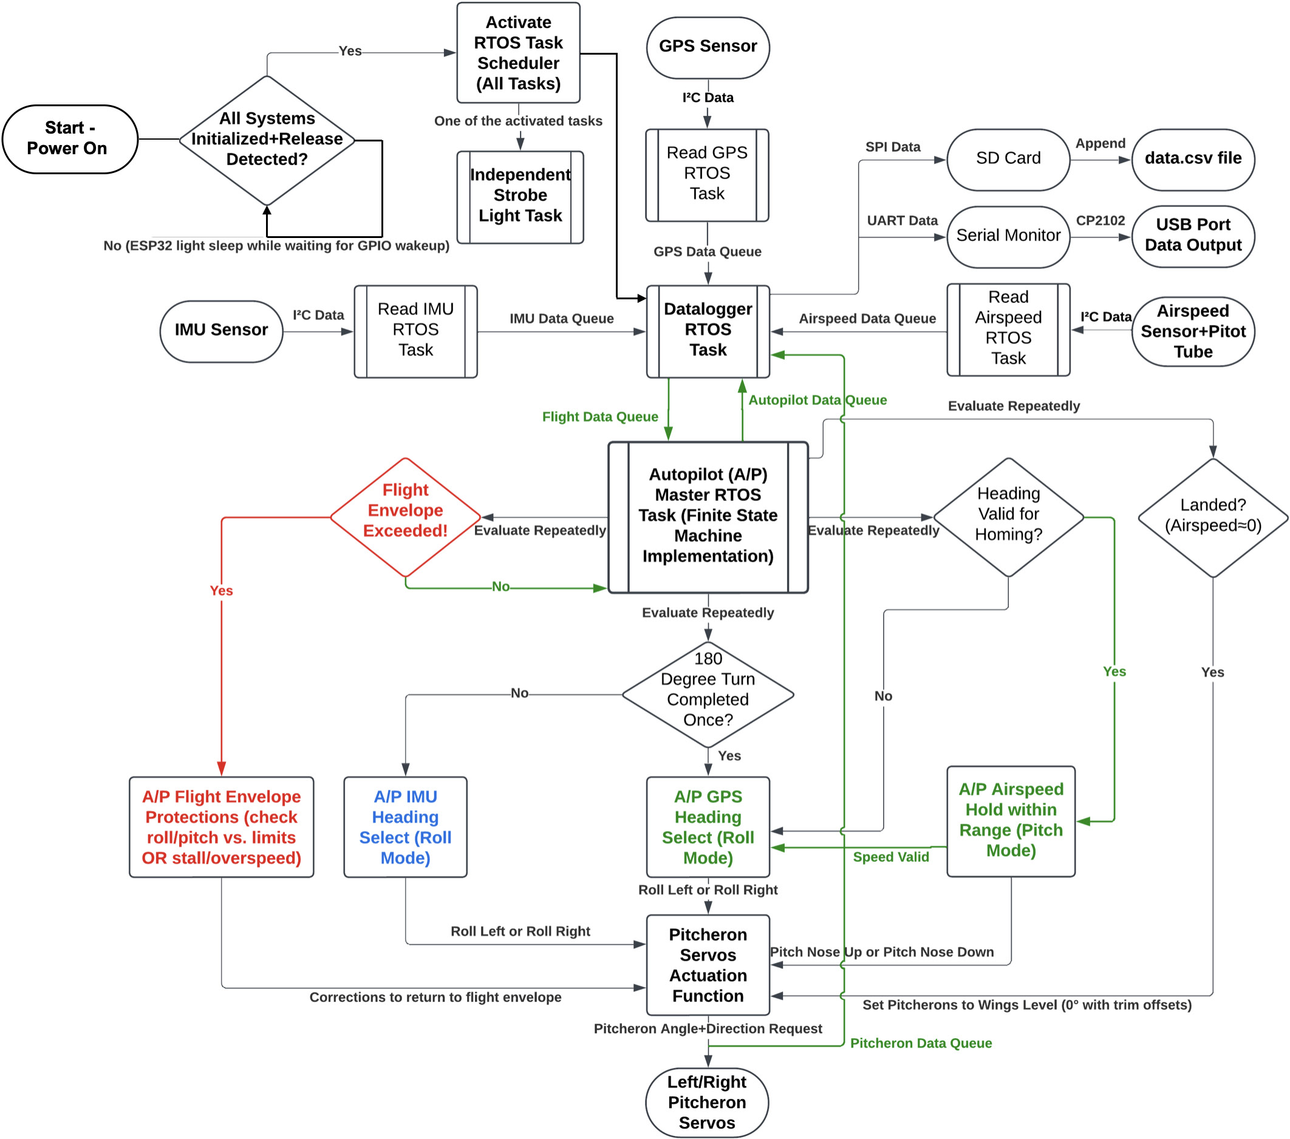
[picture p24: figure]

Figure 30: PID Control Logic Flowchart

Once release is detected, the following tasks are created and run: GPS reading, IMU reading, airspeed reading, datalogger,

autopilot, and strobe light. The strobe light task operates independently and continues indefinitely after release is detected to

ensure that the strobe LED continues flashing periodically after the glider has landed. Using FreeRTOS queues, sensor data is

transferred to a central datalogger task that manages all data logging to the SD card (in a .csv file) and/or the serial monitor. It

also routes all relevant data to the autopilot task. All sensors share an I2C mutex that only allows one sensor to access the I2C

bus at a time to prevent conflicts. Additionally, after running once, each task is suspended until all other tasks have also run to

prevent bottlenecks. After successful datalogging, all tasks are resumed before the next execution loop (with an optional delay).

The most important data collected from the IMU are roll, pitch, and yaw as Euler angles (normalized to 0-360 degrees). The

differential pressure sensor data is used to calculate airspeed, v, according to Equation 32, where ∆P is the difference between

dynamic and static pressure, and ρ is the air density updated before every flight based on local pressure, temperature, and relative

humidity. The GPS provides current latitude, longitude, and heading data used in the autopilot for homing. It also provides ground

University of Notre Dame | Page 37 of 60

speed data that can be compared to airspeed data during post-flight analysis.

v =

s
2∆P
ρ

(32)

The autopilot master task is implemented as a finite state machine that uses the flight data during each execution loop to de-

termine the current state of the aircraft. These states can be either ”performing 180 degree turn,” ”GPS homing,” ”speed-pitch

control,” or ”landed.” Each state is associated with one of the following autopilot modes: IMU heading select, GPS heading select,

or speed descent. In addition, all flight states (except for ”landed”) are associated with emergency flight envelope protection

autopilot modes for roll, pitch, and airspeed. These have the highest priority and always activate whenever a flight envelope

exceedance condition is met (regardless of state). They ensure that corrective action is taken to avoid exceeding a bank angle

limit, pitch up/down limits, and stall and overspeed protections that use pitch adjustments to increase or decrease airspeed as

required. The autopilot also sends data back to the datalogger task regarding the autopilot/flight modes, current wing angles, and

target roll/pitch/bearing. Time since release detection in seconds and a line number are also logged for easier reference during

post-flight data analysis.

The IMU heading select and GPS heading select modes are roll control modes that use the current bearing and other flight

data to determine the roll angle required to achieve the target bearing. The IMU heading select mode uses the initial yaw angle

detected on release and subtracts 180 degrees from it to determine the target yaw angle. The target roll angle is proportionally

related to the difference between the current and target yaw angles. The wing servo actuation angles are also proportionally

related to the difference between the current and target roll angles by adjusting the duty cycle of the PWM pulses. Once the

180 degree turn is complete and roll angle is near 0, the autopilot’s GPS heading select mode is activated. This mode operates

very similarly to the IMU heading select mode but uses GPS heading instead of IMU yaw angle. It continuously recalculates the

target bearing, θ, with the current and target GPS coordinates using Equation 33. Equation 33 is based on the spherical law of

cosines, where φ and λ represent latitude and longitude respectively, so that (φ2, λ2) and (φ1, λ1) are the current and target

GPS coordinates respectively. The arctan function variant used, atan2, outputs a result that lies in the first two quadrants only

(i.e. in the -180 degree to +180 degree range). The target bearing is normalized to the 0 to 360 degree range to match the GPS

heading conventions used to determine the current heading. The only edge case is when the current and target coordinates are

exactly equal, in which case the target bearing is made equal to the current bearing.

θ = arctan
sin(λ2 − λ1) · cos(φ2)
cos(φ1) · sin(φ2) − sin(φ1) · cos(φ1) · cos(λ2 − λ1)
(33)

The only regular pitch control autopilot mode is the speed descent mode, which only activates after the glider is on the correct

trajectory towards the landing zone and within roll angle limits. It is always overridden by GPS heading select whenever the

glider goes off-course, or by flight envelope protections, and has the lowest priority. This mode actuates both wings in the same

direction with an angle proportional to the pitch error, which is itself proportional to the airspeed error. For instance, if the target

airspeed is higher than the current airspeed, the target pitch will be negative (nose down) and the wings will tilt up proportionally

to achieve this pitch angle. The proportionality constants and flight envelope limits are fine-tuned based on flight testing results.

Lastly the autopilot’s landed state is activated when an airspeed of 0 ft/s is detected and simply returns both wings to their neutral

angles (wings level), disabling the autopilot to prevent unwanted actuations from draining the battery after landing. Strobe light

blinking and data collection continue until the system is powered off or reset.

University of Notre Dame | Page 38 of 60

### 5.2.2.4 Attachment and Release

Figure 31: Release Mechanism System

The X-1 test vehicle is attached to the main aircraft internally by two 3D-

printed ABS plastic servo horns, screwed into two servos attached to the

underside of a flat piece of wood. This entire platform and servo release

mechanism system, shown in Figure 31, is removable, in compliance

with AIAA rules. Each servo horn consists of a 0.4 in diameter, 1.287 in

long cylinder with four 0.268 in x 0.3 in x 0.15 in tabs that clamp around

the top plate of the X-1 test vehicle to secure it in place. When the X-1

needs to be released, the servos rotate the horns 90 degrees and the cutout on the top plate of the X-1 vehicle aligns with the

shape of the servo horn, releasing the vehicle. When the release mechanism is inserted into the plane, the servo horns slot

into cutouts on a battery platform placed 1.45 in above the floor of the plane’s fuselage, and protrude through holes on the floor

of the fuselage, allowing the glider to sit external to the plane. There is also a slot made for the vertical stabilizer of the X-1

test vehicle that allows it to protrude 0.3 in into the bottom of the fuselage. For M1 and the start of the ground mission, these

holes are covered by pieces of wood hinged to the floor of the fuselage, acting as bomb bay doors to prevent open holes in the

fuselage. This release mechanism design was selected because the servo horns are lightweight, minimally impede the airflow

underneath the main aircraft, and facilitate a secure attachment of the test vehicle to the main aircraft. The release mechanism

was strategically placed near the quarter chord of the wing to ensure that once the X-1 test vehicle was dropped, the CG of the

aircraft would be minimally affected.

### 5.2.3 Fuel Tanks

Two external fuel tanks carry a payload weight of 4 lbs each. Each fuel tank is a 24 fl-oz, commercially available HydraPak

Insulated Polar Sport plastic bottle with height of 10.5 in and diameter of 2.75 in. For the fuel tank loading material, a commercially

available material with a small particle size was needed to allow for uniform filling of the bottle. A density of approximately 4.96

slugs/ft³ was desired to satisfy the total target payload weight of 8 lbs. Type S Masonry Cement Mix, as a fine and dense material,

was an initial option, but its density of approximately 2.53 slugs/ft³
, as calculated by the team, is less than necessary. Thus, a

combination of 1/2 oz and 1/4 oz steel weights was uniformly interspersed throughout the concrete to achieve the target weight.

The team decided that this composite mix would allow for the most uniform fill and stability while still reaching the desired payload

weight. To prevent material and weight shifting during flight, the bottles are filled completely.
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

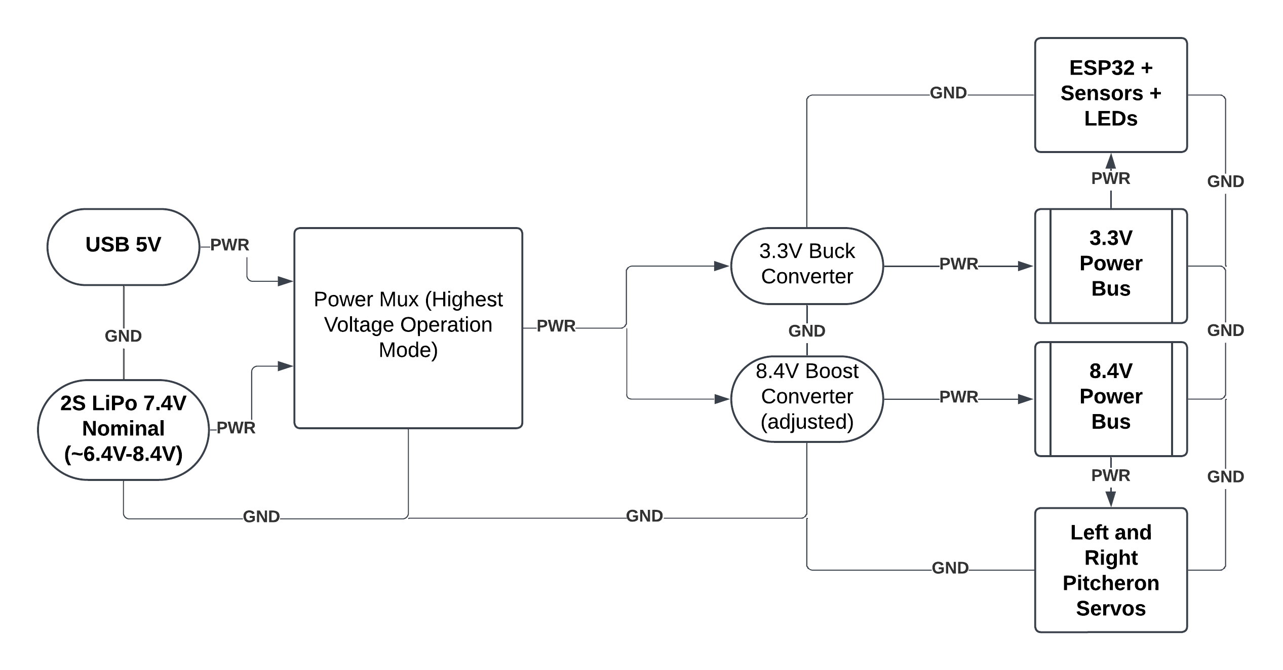
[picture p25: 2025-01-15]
DBF 24-25 System Power Path.png

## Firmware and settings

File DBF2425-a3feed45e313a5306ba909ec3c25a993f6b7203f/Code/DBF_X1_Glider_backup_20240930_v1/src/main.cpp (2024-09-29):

#include <Arduino.h>
#include "flash_filesystem.h"
#include "sensors.h"

#define DP 3 // Decimal places to record
#define SERIAL_BAUDRATE 115200
#define I2C_CLOCK_SPEED 100000 // 100 kHz
#define CONFIG_FILE_PATH "/config_DO_NOT_DELETE.sys" // File contains only filenumber of next file to be written
#define DATAFILE_LINE_BUFFER_SIZE 256
#define MAX_STORAGE_BYTES 2650000 // 4MB-1.32MB w/ extra buffer for config file in /, other folders (not /data), etc.

#define LOOP_DELAY 250 // milliseconds to wait between processing data.

#define LED_PIN 15

char datafile[32]; // Note that filename cannot be more than 31 +\0 characters long.
unsigned long line_num = 1;
unsigned long current_storage_used = 0;
bool led_state = false;

void init_serial_i2c() {
    Serial.begin(SERIAL_BAUDRATE);
    Wire.begin();
    Wire.setClock(I2C_CLOCK_SPEED);
}

void float_data_to_string(float* data, int data_size, char * output_string, bool serial_print=false) {
    static unsigned long time_epoch = micros();
    unsigned long current_time = micros();
    sprintf(output_string, "%lu,%lu,%.*f,%.*f,%.*f,%.*f,%.*f\n", \
    line_num, \
    (current_time-time_epoch), \
    // Raw Diff Pressure
    DP, data[2], \
    // Raw Airspeed
    DP, data[3], \
    // Temperature
    DP, data[4]);
    if(serial_print) {
        Serial.print(output_string);
    }
}

void setup() {
    init_serial_i2c();
    pinMode(LED_PIN, OUTPUT);
    delay(3000);
    init_fs(); // Initialize littlefs
    init_ms4525do(); // Initialize Diff Pressure Sensor for Airspeed
    digitalWrite(LED_PIN, true);
    delay(2000);
    digitalWrite(LED_PIN, false);

    current_storage_used = list_files("/data");

    const char csv_header[] = "Line_No.,Time(us),Corr_DP(Pa),Corr_Airspeed(m/s),DP(Pa),Airspeed(m/s),Temperature(C)\n";
    int current_datafile_number;
    int next_datafile_number;
    const char current_datafile_number_str[] = "000";
    const char next_datafile_number_str[] = "000";
    // Filenumber Management
    read_file(CONFIG_FILE_PATH, current_datafile_number_str, true, true); // Read string filenumber
    sscanf(current_datafile_number_str, "%d", &current_datafile_number); // Convert filenumber to int
    next_datafile_number = current_datafile_number;
    next_datafile_number++; // Increment filenumber for next reboot
    if (next_datafile_number > 999) {
        next_datafile_number = 0; // Loopback and overwrite
    }
    sprintf((char*)next_datafile_number_str, "%03d", next_datafile_number); // Convert int to padded string
    write_file(CONFIG_FILE_PATH, next_datafile_number_str); // Store Padded string in CONFIG file.

    current_storage_used += strlen(csv_header);
    if (current_storage_used > MAX_STORAGE_BYTES) {
        while(1) {
            Serial.println("STORAGE FULL! Please clear up some space.");
            digitalWrite(LED_PIN, false);
        }
    }

    sprintf((char*)datafile, "/data/data%03d.csv", current_datafile_number); // Create filepath
    write_file(datafile, csv_header, false); // Write file header
}

void loop() {
    char csv_output_string[DATAFILE_LINE_BUFFER_SIZE] = "";
    const int ms4525do_field_count = 5; // Raw + Corrected Airspeed & Pressure + Temperature
    const int imu_field_count = 12; // Acce, Gyro, Mag, Orientation
    float ms4525do_output[ms4525do_field_count] = {0.0}; // Initialize to 0 every loop time.
    float imu_output[imu_field_count] = {0.0};
    read_ms4525do(ms4525do_output);
    float_data_to_string(ms4525do_output,ms4525do_field_count,csv_output_string, false);
    // Serial.println(datafile);
    // Serial.println(csv_output_string);
    current_storage_used += strlen(csv_output_string);
    if (current_storage_used > MAX_STORAGE_BYTES) {
        while(1) {
            Serial.println("STORAGE FULL! Please clear up some space.");
            digitalWrite(LED_PIN, false);
        }
    }
    append_file(datafile, csv_output_string, false);
    line_num++;
    led_state = ~led_state;
    digitalWrite(LED_PIN, led_state);
    delay(LOOP_DELAY);
}

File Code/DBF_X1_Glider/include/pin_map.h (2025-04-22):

#ifndef PIN_MAP_H
#define PIN_MAP_H

// For datalogger (SPI pins)
#define SD_CS 5
#define SD_MISO 25
#define SD_MOSI 26
#define SD_SCK 27

// For all sensors (I2C pins)
#define SDA_PIN 21
#define SCL_PIN 22

// Outputs (LEDs+Servos)
#define BUILTIN_LED_PIN 2

#define RELEASE_DET_PIN 4
#define STROBE_LED_PIN 20

// Separate left and right servo pin defs
#define SERVO_L_PIN 14
#define SERVO_R_PIN 13

#endif

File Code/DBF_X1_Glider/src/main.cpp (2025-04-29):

#include <Arduino.h>
//#include "soc/soc.h"
//#include "soc/rtc_cntl_reg.h"
#include "esp_sleep.h"
#include "tasks.h"
#include "queues.h"
#include "semaphores.h"
#include "sensors.h"
#include "datalogger.h"
#include "pitcheron_servos.h"
#include "trim_servos.h"
#include "strobe.h"
#include "autopilot.h"
#include "pin_map.h"

#define RELEASE_INIT true // Wait for release before running main code
#define SERIAL_LOG true // Log Data to Serial
#define SD_LOG true // Log Data to SD Card file (failsafe for SD card popping out if true is included. If that happens, true constant is ignored.)
#define TRIM_SERVOS false // Choose whether to run this program in regular or servo trimming mode
#define SERVO_ACTUATION_TESTS true // Perform pitcheron servo tests during initialization? (ignored if TRIM_SERVOS=true)
#define BOOTUP_DELAY 2000 //ms
#define INSTALL_DEBOUNCE_DELAY 250 //ms
#define INSTALL_DELAY 10000
#define RELEASE_DELAY 250 //ms
#define THROW_DELAY 5000 //ms

void setup() {
    delay(BOOTUP_DELAY);
    //WRITE_PERI_REG(RTC_CNTL_BROWN_OUT_REG, 0);
    pinMode(RELEASE_DET_PIN, INPUT);
    esp_sleep_enable_ext0_wakeup((gpio_num_t)RELEASE_DET_PIN, HIGH); 
    init_low_level_hw();
    init_strobe();
    init_queues();
    init_semaphores();
    init_all_sensors();
    
    if (TRIM_SERVOS == false) init_servos(SERVO_ACTUATION_TESTS);
    else trim_servos(); // Note: this instruction is blocking. No further lines of code in this file will execute and RTOS Scheduler never starts.

    init_SD(SERIAL_LOG, SD_LOG); // FORMAT SD CARD TO FAT32 BEFORE FIRST USE
    
    if (RELEASE_INIT) {
        Serial.println("All Systems Initialized. Waiting for GPIO 19 release detection (HIGH=>LOW=>HIGH)...");
        digitalWrite(BUILTIN_LED_PIN, LOW);
        while (true) {
            while (true) {
                if (digitalRead(RELEASE_DET_PIN) == HIGH) delay(INSTALL_DEBOUNCE_DELAY);
                else {
                    delay(INSTALL_DEBOUNCE_DELAY);
                    if (digitalRead(RELEASE_DET_PIN) == LOW) break;
                }
            }

            digitalWrite(BUILTIN_LED_PIN, HIGH);
            delay(INSTALL_DELAY);
            if (digitalRead(RELEASE_DET_PIN) == HIGH) {
                digitalWrite(BUILTIN_LED_PIN, LOW);
                delay(250);
                digitalWrite(BUILTIN_LED_PIN, HIGH);
                continue;
            }
            else break;
        }
        digitalWrite(BUILTIN_LED_PIN, LOW);

        while (digitalRead(RELEASE_DET_PIN) == LOW) {
            esp_light_sleep_start();
            delay(RELEASE_DELAY); // for debouncing release detection magnet
        }
    }
    delay(THROW_DELAY);
    init_tasks();
    Serial.println("All Systems ONLINE! All Tasks Started Successfully! RTOS Task Scheduler RUNNING!\n");

}

void loop() {
    ;//vTaskStartScheduler();
}

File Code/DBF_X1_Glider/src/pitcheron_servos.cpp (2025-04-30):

#include <Arduino.h>
#include <ESP32Servo.h>
#include "pin_map.h"
#include "pitcheron_servos.h"
#include "queues.h"

#define DISABLE_SERVOS false
#ifndef DISABLE_SERVOS
#define DISABLE_SERVO_L false
#define DISABLE_SERVO_R false
#endif

#ifdef DISABLE_SERVOS
#define DISABLE_SERVO_L DISABLE_SERVOS
#define DISABLE_SERVO_R DISABLE_SERVOS
#endif
// Basic Assumption: Pitcheron Angle = Servo Angle
// https://cdn.shopify.com/s/files/1/0570/1766/3541/files/X08H_V6.0_Technical_Specifcation.pdf?v=1700472376
// https://kstservos.com/collections/glider-wing-servos/products/x08h-plus-horizontal-lug-servo-5-3kg-cm-0-09s-9-5g-8mm

// Servos l and r are connected to left and right pitcherons as viewed from behind the glider.
// CW_CONVENTION: Clockwise = Positive Angle, Counterclockwise = Negative Angle. Set CONVENTION to -1 if opposite (still assumes 2 identical servos)
#define CW_CONVENTION -1 // 1=Clockwise Positive, -1=Counterclockwise Positive

// CG_CONVENTION: Determine whether fully assembled glider CG is behind or in front of the pitcherons (wingtip test!)
#define CG_CONVENTION -1 // 1 = Pitcherons point up, nose goes down (pitcherons behind CG, like elevators). -1 = Pitcherons point up, nose goes up (pitcherons in front of CG).

// Note: center would be 0 degrees left and right in code, but may not be the case in real life. Trim offset added to center
#define RAW_TRIM_L 9 // deg. Set this to whatever angle must be requested in independent servo tests (actuate_servo_l) to center left servo when testing (regardless of CONVENTION).
#define RAW_TRIM_R 7 // deg. Set this to whatever angle must be requested in independent servo tests (actuate_servo_r) to center right servo when testing (regardless of CONVENTION).
// Define Servo Physical Limits
#define MIN_SERVO_us 1000 // us
#define MAX_SERVO_us 2000 // us
#define PWM_FREQUENCY 333 // Hz
#define INITIAL_ANGLE 14

#define ACTUATION_DELAY_ms 1000 // How long to wait after each actuation test

Servo left_servo;
Servo right_servo;

void init_servos_trim(void) {
    Serial.println("Initializing Servos...");
    if (DISABLE_SERVO_L) Serial.println("Left Servo Disabled. Code will run as if it is enabled, but without physically initializing/actuating.");
    if (DISABLE_SERVO_R) Serial.println("Right Servo Disabled. Code will run as if it is enabled, but without physically initializing/actuating.");
	if (!DISABLE_SERVO_L) ESP32PWM::allocateTimer(0); // Allocate timer for both servos
	if (!DISABLE_SERVO_R) ESP32PWM::allocateTimer(1); // Allocate timer for both servos
    if (!DISABLE_SERVO_L) left_servo.setPeriodHertz(PWM_FREQUENCY);    // 333 Hz servo
    if (!DISABLE_SERVO_R) right_servo.setPeriodHertz(PWM_FREQUENCY);    // 333 Hz servo
    if (!DISABLE_SERVO_L) left_servo.attach(SERVO_L_PIN, 900, 2100); // Attach left servo to pin
    if (!DISABLE_SERVO_R) right_servo.attach(SERVO_R_PIN, 900, 2100); // Attach right servo to pin
    Serial.println("Servo Initialization Complete. Start Trimming."); 
}

// This function maps angles to microseconds (PWM width) based on servo datasheet
int angle2us(int angle, int angle_min, int angle_max, int us_min, int us_max) {
    if (angle < angle_min) angle = angle_min; // Handle limit
    else if (angle > angle_max) angle = angle_max; // Handle limit
    return us_min + ((angle - angle_min) * (us_max - us_min)) / (angle_max - angle_min);
}

void actuate_servo_l(int raw_angle_servo_l) {
    if (!DISABLE_SERVO_L) left_servo.writeMicroseconds(angle2us(raw_angle_servo_l, MIN_SERVO_ANGLE, MAX_SERVO_ANGLE, MIN_SERVO_us, MAX_SERVO_us));
}

void actuate_servo_r(int raw_angle_servo_r) {
    if (!DISABLE_SERVO_R) right_servo.writeMicroseconds(angle2us(raw_angle_servo_r, MIN_SERVO_ANGLE, MAX_SERVO_ANGLE, MIN_SERVO_us, MAX_SERVO_us));
}

// This function initializes the servos, checks range of travel, and then centers servos
void init_servos(bool actuation_test = true) {
    Serial.println("Initializing Servos...");
    if (DISABLE_SERVO_L) Serial.println("Left Servo Disabled. Code will run as if it is enabled, but without physically initializing/actuating.");
    if (DISABLE_SERVO_R) Serial.println("Right Servo Disabled. Code will run as if it is enabled, but without physically initializing/actuating.");
	if (!DISABLE_SERVO_L) ESP32PWM::allocateTimer(0); // Allocate timer for both servos
	if (!DISABLE_SERVO_R) ESP32PWM::allocateTimer(1); // Allocate timer for both servos
    if (!DISABLE_SERVO_L) left_servo.setPeriodHertz(PWM_FREQUENCY);    // 333 Hz servo
    if (!DISABLE_SERVO_R) right_servo.setPeriodHertz(PWM_FREQUENCY);    // 333 Hz servo
    if (!DISABLE_SERVO_L) left_servo.attach(SERVO_L_PIN, 900, 2100); // Attach left servo to pin
    if (!DISABLE_SERVO_R) right_servo.attach(SERVO_R_PIN, 900, 2100); // Attach right servo to pin

    // Set servos to 0 position
    Serial.printf("Centering LEFT servo centered with trim @%ddeg.\n", RAW_TRIM_L);
    actuate_servo_l(RAW_TRIM_L+0);
    Serial.printf("Centering RIGHT servo centered with trim @%ddeg.\n", RAW_TRIM_R);
    actuate_servo_r(RAW_TRIM_R+0);
    Serial.println("Servo Initialization Complete! Verify both pitcherons are now correctly trimmed/centered.");
    if (CW_CONVENTION == -1) Serial.println("Note: Using alternate convention for angles (+ => counterclockwise, - => clockwise).");
    else if (CW_CONVENTION != 1) Serial.println("INVALID CW_CONVENTION SPECIFIED! STOP! Roll control will be scaled incorrectly!");
    delay(ACTUATION_DELAY_ms);
    if (actuation_test == true) {
        Serial.println("Testing Servos... Observe movement carefully to verify correct actuation/response.");
        // If both servos turn counterclockwise or clockwise, Pitcherons = Ailerons
        // If one turns clockwise and the other counterclockwise, Pitcherons = Elevator

        // Turn both servos in same direction (counterclockwise: counter-rotating pitcherons). Left pitcheron points down, right points up (roll left)
        actuate_servo_l(RAW_TRIM_L+(SERVO_MIN_ALLOWED*CW_CONVENTION));
        actuate_servo_r(RAW_TRIM_R+(SERVO_MIN_ALLOWED*CW_CONVENTION));
        Serial.printf("Test #1/6: Confirm that LEFT pitcheron points DOWN and RIGHT pitcheron points UP (both@min allowed deflection = %ddeg).\n", SERVO_MIN_ALLOWED);
        delay(ACTUATION_DELAY_ms);

        // Turn both servos in same direction (clockwise: counter-rotating pitcherons). Left pitcheron points up, Right points down (roll right)
        actuate_servo_l(RAW_TRIM_L+(SERVO_MAX_ALLOWED*CW_CONVENTION));
        actuate_servo_r(RAW_TRIM_R+(SERVO_MAX_ALLOWED*CW_CONVENTION));
        Serial.printf("Test #2/6: Confirm that LEFT pitcheron points UP and RIGHT pitcheron points DOWN (both@max allowed deflection = %ddeg).\n", SERVO_MAX_ALLOWED);
        delay(ACTUATION_DELAY_ms);
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

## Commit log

2024-09-14 IMU and Diff Pressure Sensor Unit Tests
2024-09-17 Refactored sensor code for modularity. Also set up filesystem for flash memory.
2024-09-18 Completed IMU & Pitot Tube Unit Testing.
2024-09-23 Completed full data collection code (for airspeed sensor in main)
2024-09-23 Added LED indication
2024-10-02 Full RTOS Flight Data Collection (-SD Card) Software with sample rate optimizations (stack size+dual core)
2024-10-02 Fixed and Optimized GPS
    [datalogger.cpp, main.cpp, sensors.cpp]
2024-10-02 Minor Airspeed Corrections & better GPS Synchronization
    [datalogger.cpp, sensors.cpp, tasks.cpp]
2024-10-03 Bug fix for data collection
    [datalogger.cpp, main.cpp]
2024-10-03 minor bug fix with SD data
    [datalogger.cpp, main.cpp]
2024-10-03 improved .csv header & gyro output => deg/s from rad/s
2024-10-03 minor error handling improvement
    [datalogger.cpp, sensors.cpp]
2024-10-04 corrected euler angle direction with negative signs (pitch/yaw)
    [datalogger.cpp, sensors.cpp]
2024-10-04 Optimized GPS sampling, fixed GPS hour timezone bug, and added extra GPS fix lost/regained Serial info
    [datalogger.cpp, sensors.cpp]
2024-10-04 Updated GPS min. delay threshold to 0.1s after setting rate to 25Hz
2024-10-04 Increased I2C speed to 400kHz (max)
2024-10-05 Sped up GPS data collection and added airspeed=0 if <5m/s (inaccurate airspeed at low speeds). Baudrate increased to fix serial buffer filling issues
    [datalogger.cpp, sensors.cpp]
2024-10-06 Flight Data
    [Data_20241006Flight1.csv, Data_20241006Flight2.csv, RawData_20241006Flight1.csv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]
2024-10-08 Changed units from m to feet (imu,pitot)
    [Data_20241006_Flight1.csv, Data_20241006_Flight2.csv, RawData_20241006_Flight1.csv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]
2024-11-12 Starting PCB Design
    [BOM.xlsx, DBF2425_PCB.kicad_pcb, DBF2425_PCB.kicad_sch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]
2024-12-05 Servo code mostly complete with datalogging. Autopilot code remains.
2024-12-06 Wrote in header template for autopilot and normalized imu yaw from +-180 to 0-360 to match GPS heading
2024-12-07 Autopilot ready. Limits, targets, and proportionality constants missing.
    [ABP2_test.cpp, airspeed_test.cpp, autopilot.cpp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]
2024-12-07 Code v2 complete. Autopilot with IMU only.
2025-01-15 GPS Homing Code complete. Code ready for deployment (PID/envelope constants TBD)
    [Data_20241006_Flight1.csv, Data_20241006_Flight2.csv, RawData_20241006_Flight1.csv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]
2025-02-12 Fully Functional Autopilot with PCB v2. Strobe LEDs & Release Detection TBD
2025-02-15 Strobe LED and release detection code with light sleep done. Minor fix to use GPS heading in autopilot. Flight ready.
    [autopilot.cpp, datalogger.cpp, main.cpp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]
2025-02-25 Minor updates to flags + flight data (DAC/Glider)
    [DAC_data_20250217.csv, Glider_data_20250217.csv]
2025-03-23 Bug fixes and minor enhancements
    [BOM.xlsx, DBF2425_PCB.kicad_pcb, DBF2425_PCB.kicad_sch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]
2025-03-23 Minor bearing change update (-180=>+180)
2025-04-03 Updated LED code and servo limits
    [data007.csv, data008.csv, data015.csv]
2025-04-22 Tucson Final Flight Code
    [Data_20250411.csv]
2025-04-25 servo enable
2025-04-30 unsigned int => int made explicit to avoid compiler implicit fix
    [pitcheron_servos.cpp]
